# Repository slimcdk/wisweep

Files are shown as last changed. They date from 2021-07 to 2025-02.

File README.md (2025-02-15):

Feel free to support me and the development I do!

<a href="https://www.buymeacoffee.com/slimcdk" target="_blank">Buy Me A Coffee</a>

# WiSweep

Compact WiFi and Bluetooth (5.0) / ZigBee NEMA17 stepper controller featuring stall detection and ultra silent operation. Supply 5-36V upto 3A.

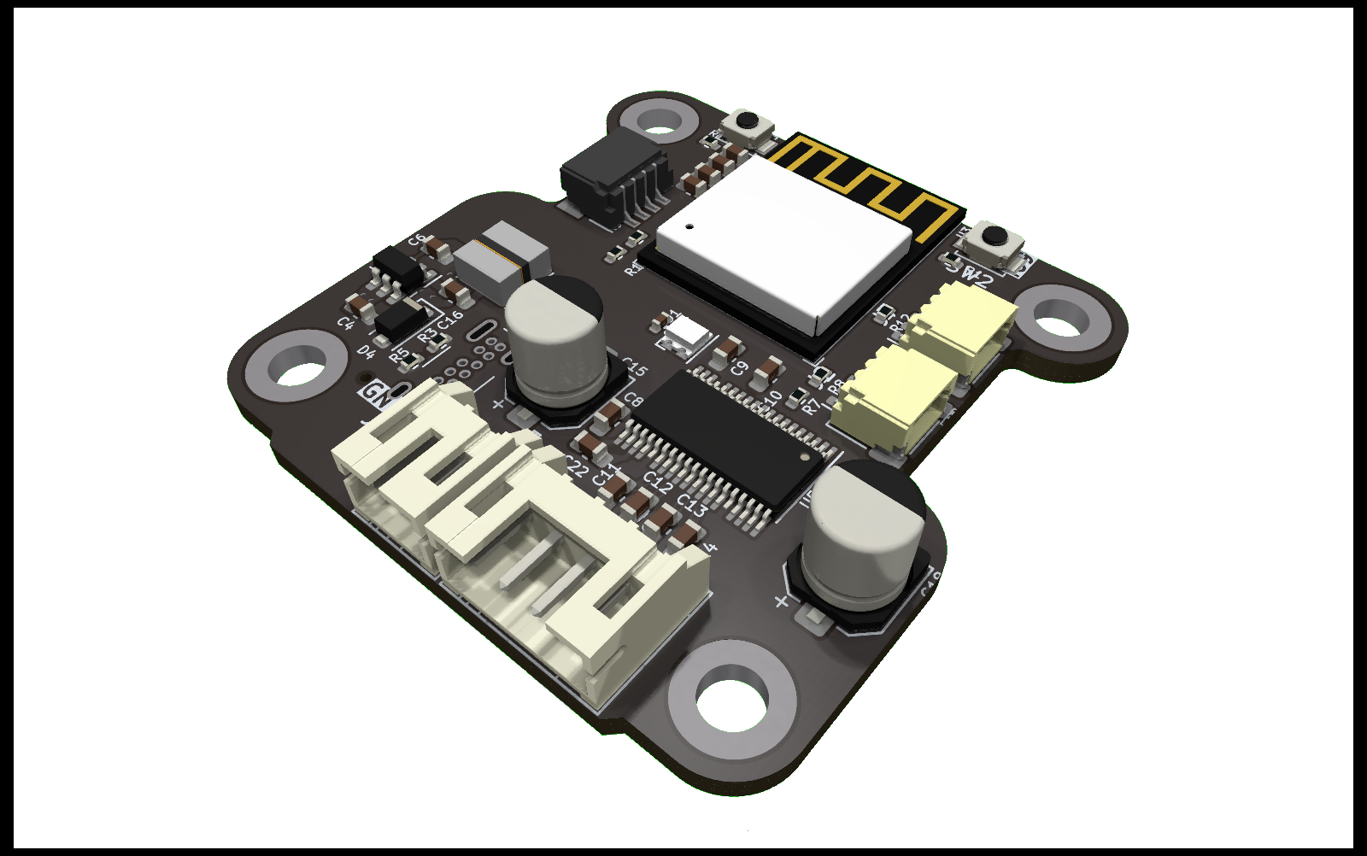
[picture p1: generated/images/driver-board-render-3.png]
the picture


## Production files



## Contribution

Clone repository and fetch submodules

```bash
$ git clone --recursive-submodules git@github.com:slimcdk/wisweep.git
```

## Versioning

Revisions are controlled through git tags such any production easily can be traced back to a commit containing everything. Complete sets of compatible schematics, PCB layouts, documentations, 3D models etc will all stay together under same tag in the source history.

---

## Software uses

* https://www.kicad.org/
* https://www.freecadweb.org/
* https://github.com/features/actions
  * https://github.com/INTI-CMNB/KiBot
* https://code.visualstudio.com/
  * https://marketplace.visualstudio.com/items?itemName=ms-vscode-remote.remote-containers

## Notes

### Parts

`VKMB1001H330MV` can be hard to source - `VKMB1001H220MV` (22µF variant) is an alternative.

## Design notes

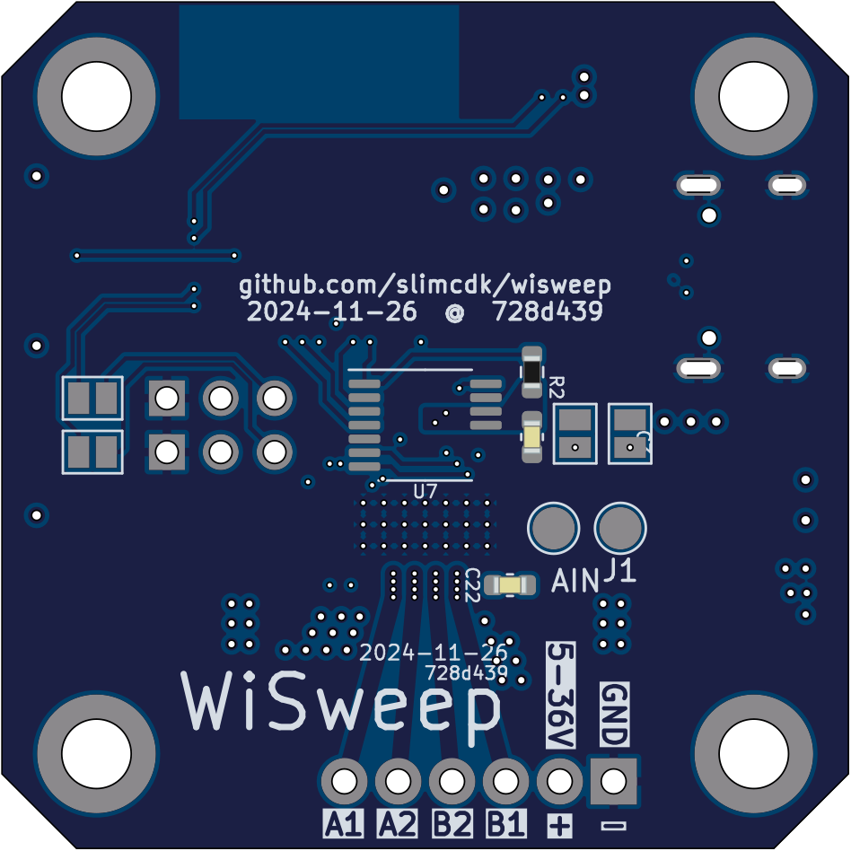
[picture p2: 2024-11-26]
generated/images/driver-board-bottom-view.png

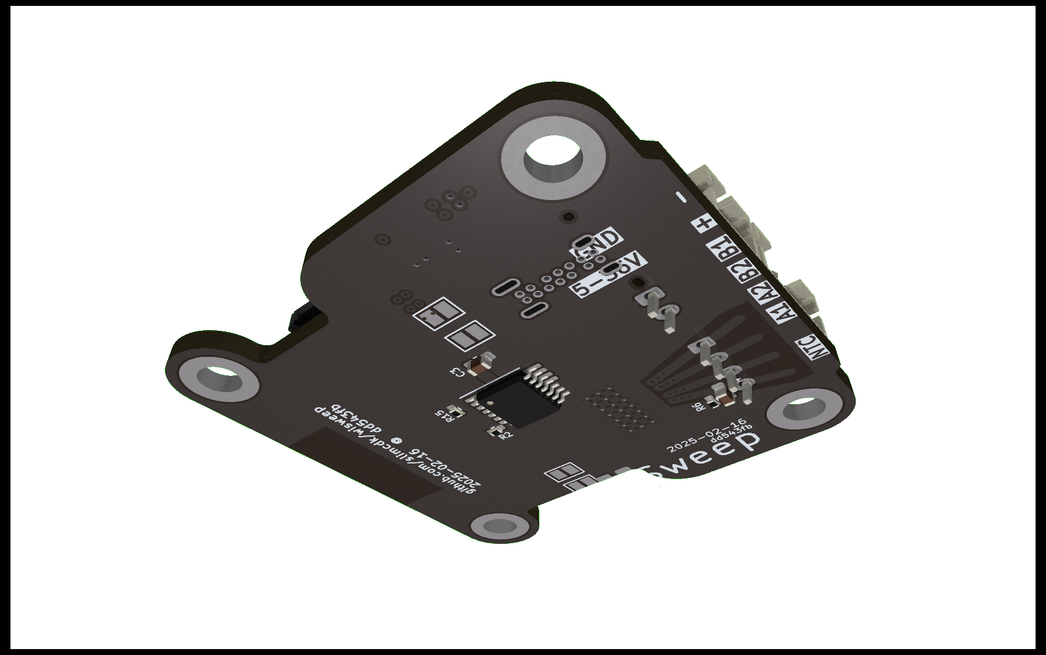
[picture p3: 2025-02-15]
generated/images/driver-board-render-5.png

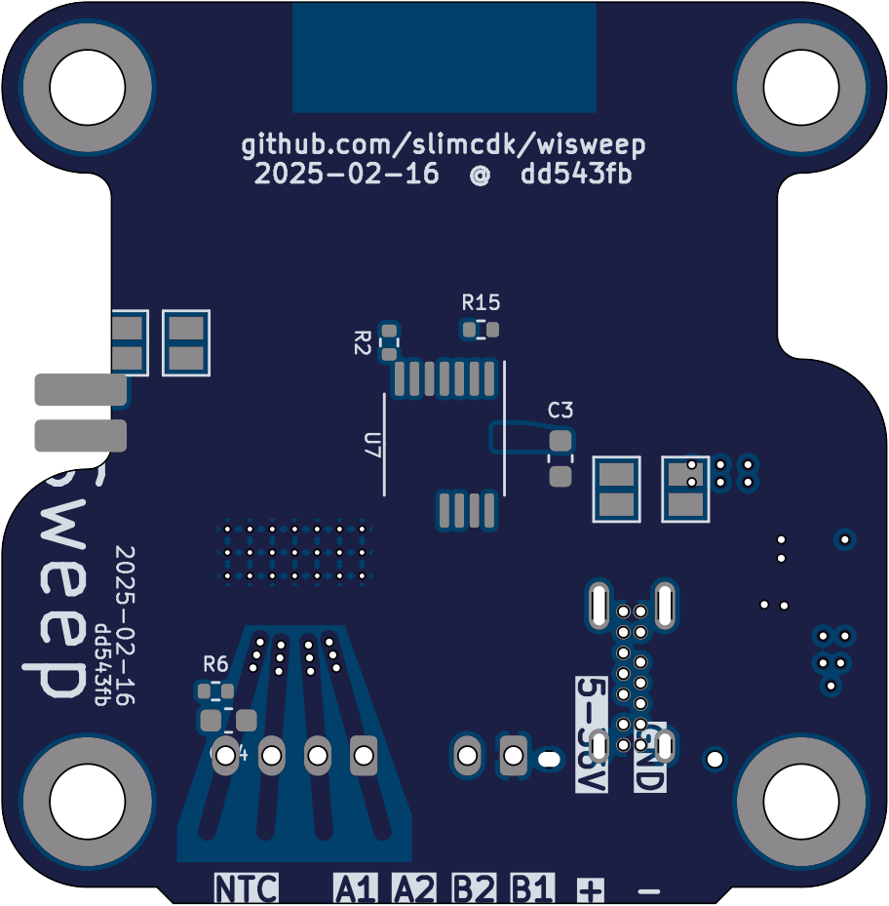
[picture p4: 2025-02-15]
generated/images/driver-board-bottom-view-no-comps.png

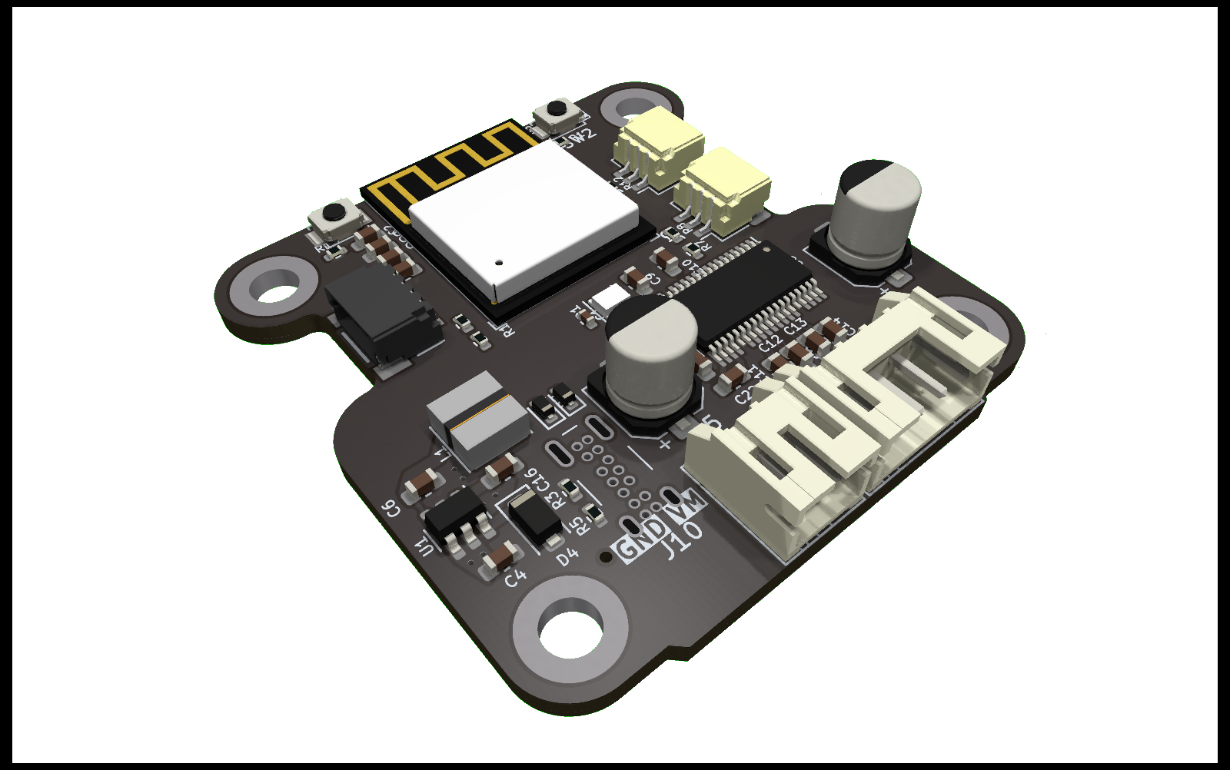
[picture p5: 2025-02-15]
generated/images/driver-board-render-4.png

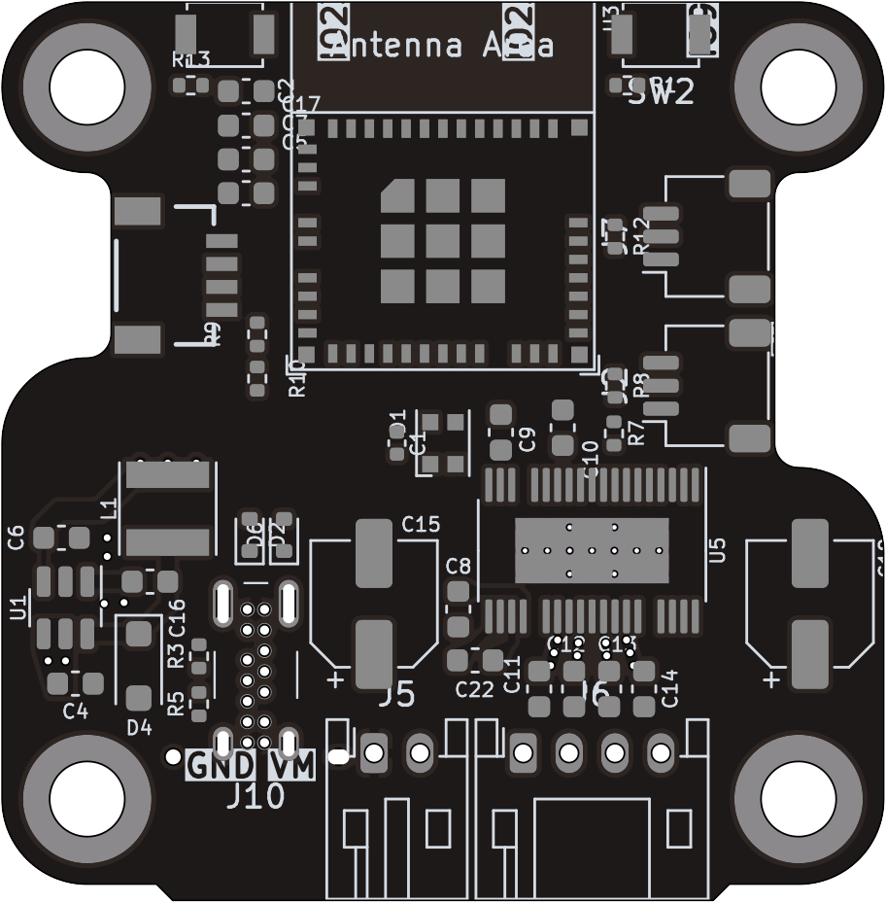
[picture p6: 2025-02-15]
generated/images/driver-board-top-view-no-comps.png

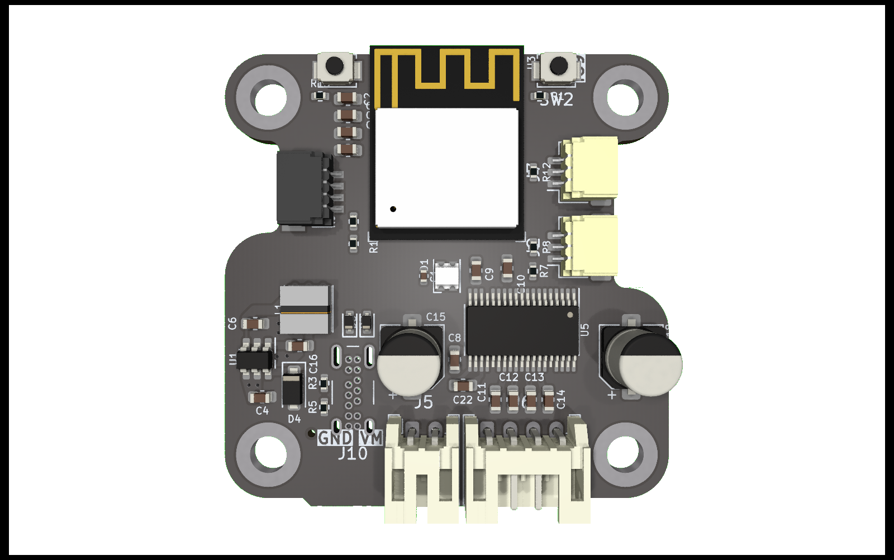
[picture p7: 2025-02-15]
generated/images/driver-board-render-1.png

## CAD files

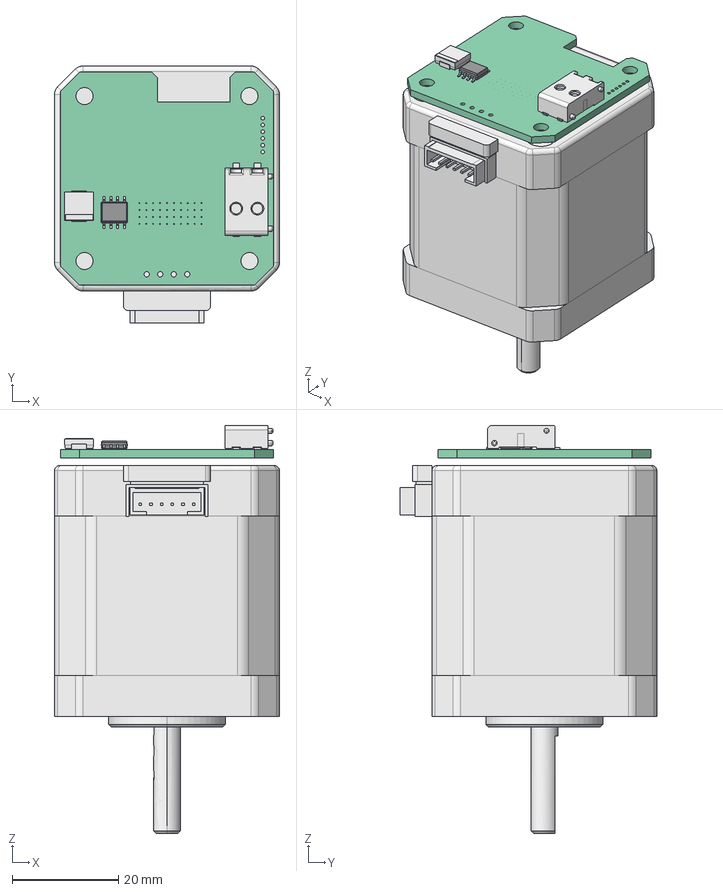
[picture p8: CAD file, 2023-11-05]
mechanics/assembly.FCStd
42.3 x 48.3 x 76.7 mm
Pulsivo_Stepper_17HS8401S
Pcb_5eb1
J1_C-2834006-2_000060e6b506[2]
BODY-SO
LEAD-SO
LEAD-SO001
LEAD-SO002
LEAD-SO003
LEAD-SO004
LEAD-SO005
LEAD-SO006
LEAD-SO007
THERMALPAD-SO

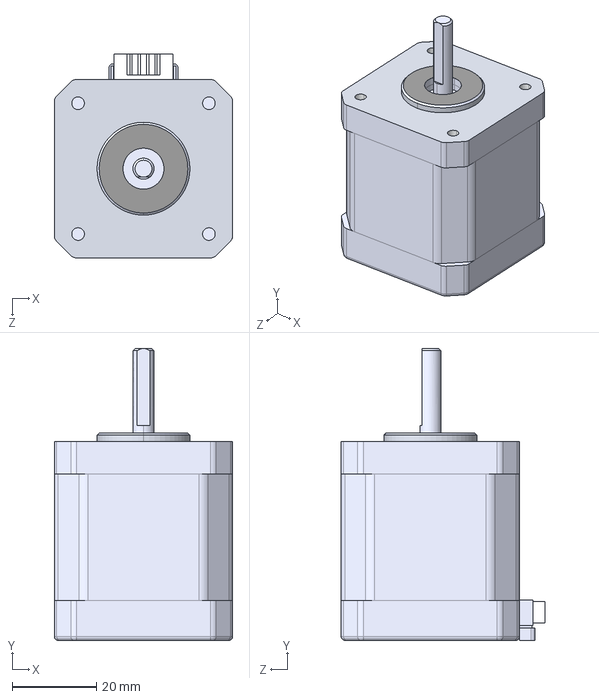
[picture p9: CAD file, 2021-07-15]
dependencies/3d-models/nema17-model/Pulsivo_Stepper_17HS8401S.IGS
42.3 x 69.2 x 48.3 mm

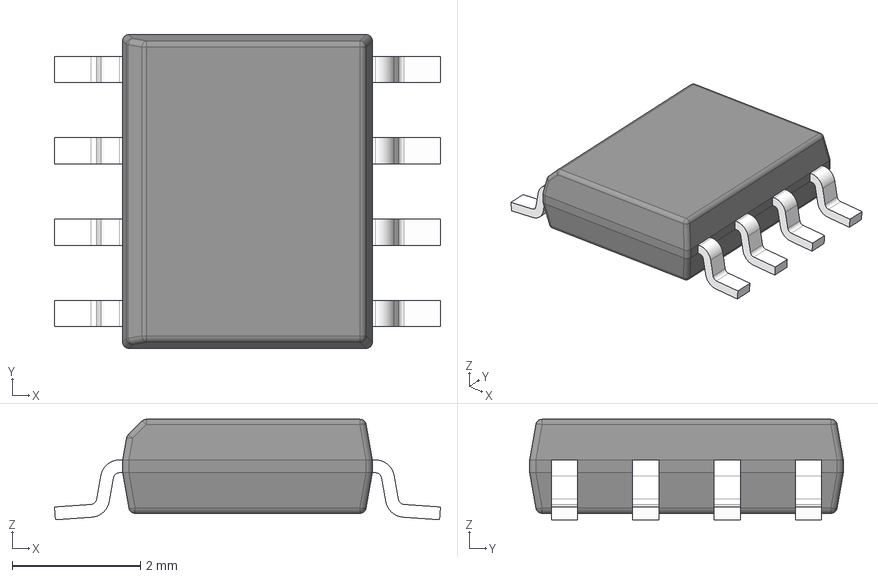
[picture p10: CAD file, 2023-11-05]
dependencies/3d-models/DDA0008B.stp
6.03 x 4.90 x 1.57 mm
BODY-SO
LEAD-SO x 8
THERMALPAD-SO

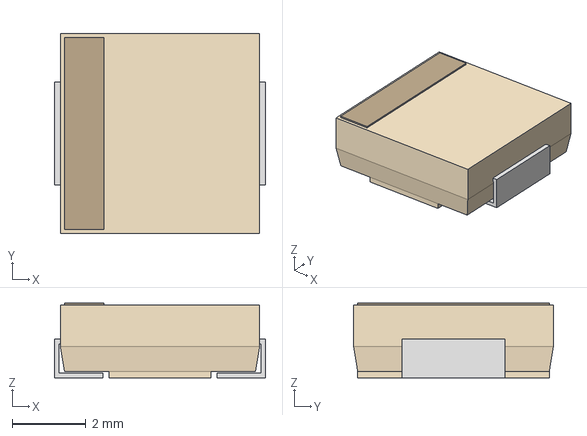
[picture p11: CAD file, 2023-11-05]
dependencies/3d-models/IND_IHLP_2020_BZ_VIS.step
5.74 x 5.44 x 2.03 mm

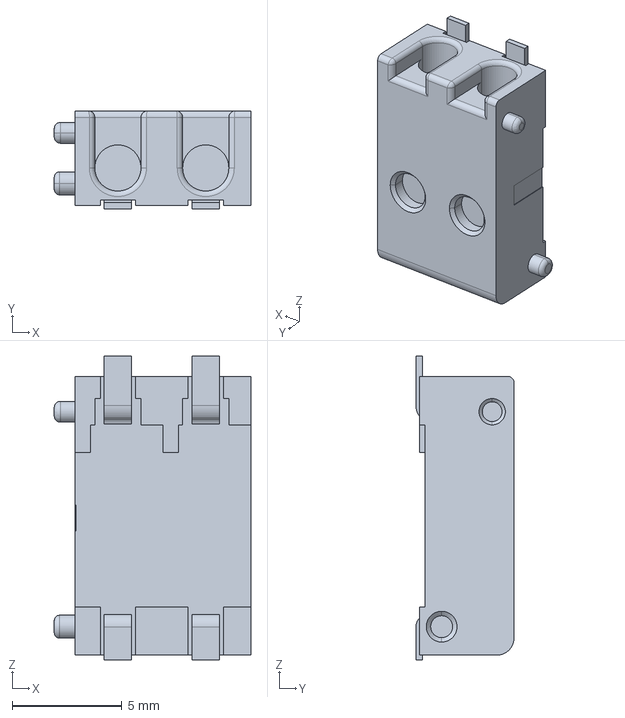
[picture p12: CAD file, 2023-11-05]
dependencies/3d-models/c-2834006-2-c-3d.stp
8.95 x 4.47 x 13.8 mm

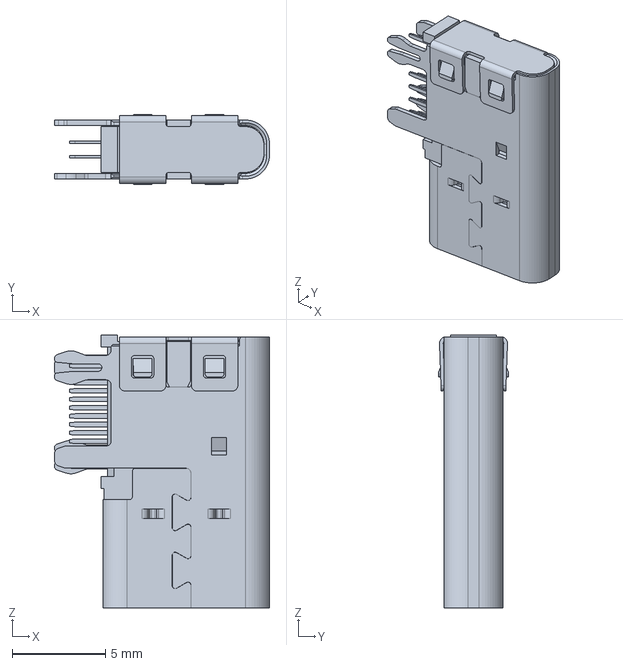
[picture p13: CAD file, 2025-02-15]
dependencies/3d-models/2169890001.stp
11.5 x 3.76 x 14.7 mm

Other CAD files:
dependencies/3d-models/nema17-model/Pulsivo_Stepper_17HS8401S.STL

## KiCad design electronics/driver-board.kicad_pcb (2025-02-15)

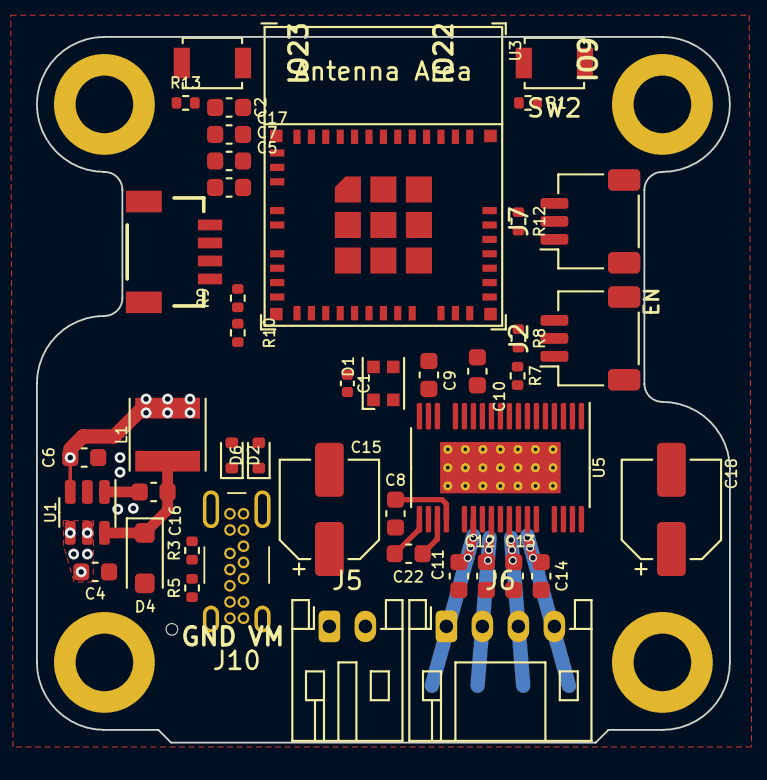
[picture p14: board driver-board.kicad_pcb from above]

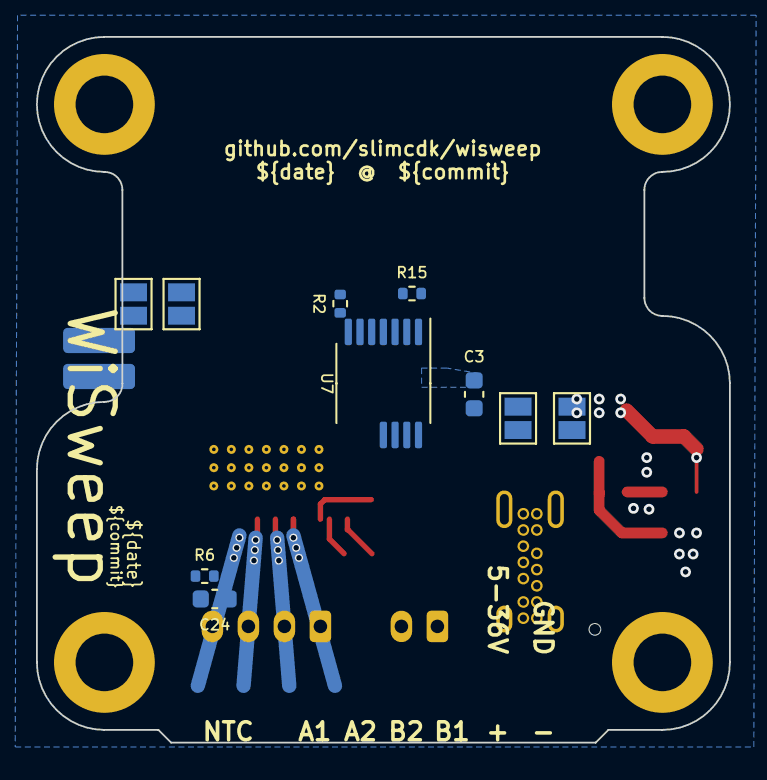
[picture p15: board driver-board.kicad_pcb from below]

Board: 4 copper layers, 38.5 x 39.2 mm, 58 parts (11 on the bottom side), 42 nets.

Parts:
C1: 100nF; C_0402_1005Metric
C2, C7, C8, C13, C14: 1µF; C_0603_1608Metric
C3, C9, C11, C12, C16, C17, C24: 100nF; C_0603_1608Metric
C4, C10: 2.2µF; C_0603_1608Metric
C5, C6: 10µF; C_0603_1608Metric
C15, C18: 33µF; CP_Elec_5x5.9
C22: 22nF; C_0603_1608Metric
D1: WS2812B; LED_WS2812B-2020_PLCC4_2.0x2.0mm
D2, D6: LESD5D5; D_SOD-523
D4: DS210W; D_SOD-123F
H1, H2, H3, H4: M3 MountingHole; MountingHole_3.2mm_M3_DIN965_Pad
J1: Conn_01x02; PinHeader_1x02_P2.00mm_Vertical_SMD_Pin1Left
J2, J7: Conn_01x03; JST_SH_SM03B-SRSS-TB_1x03-1MP_P1.00mm_Horizontal
J4: Qwiic_RA; JST_SMD_1.0mm-4_RA
J5: Conn_01x02; JST_PH_S2B-PH-K_1x02_P2.00mm_Horizontal
J6: Conn_01x04; JST_PH_S4B-PH-K_1x04_P2.00mm_Horizontal
J10: USB_C_Receptacle_USB2.0; USB_C_GT-USB-7036A
JP1, JP2, JP3, JP4: Jumper_2_Open; SolderJumper-2_P1.3mm_Open_Pad1.0x1.5mm
L1: 6.8µH; L_Vishay_IFSC-1515AH_4x4x1.8mm
R1, R2, R6, R8, R9, R10, R12, R13, R15: 10k; R_0402_1005Metric
R3, R5: 5k1; R_0402_1005Metric
R7: 12k; R_0402_1005Metric
SW1, SW2: SW_Push; SW_SPST_B3U-1000P
U1: LMR16006YQ3; SOT-23-6
U3: ESP32-C6-MINI-1/U; ESP32-C6-MINI-1
U5: TMC5240-TSSOP38; TSSOP-38_4.4x9.7mm_P0.5mm
U7: AS5047D; TSSOP-14_4.4x5mm_P0.65mm

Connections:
+3V3: C1.1, C3.2, C5.2, C6.2, C7.2, C9.2, C17.2, D1.1 (VDD), J2.2, J4.2, J7.2, L1.2, R1.2, R2.2, R6.2, R8.2, R9.2, R10.2, R12.2, R13.2, U1.3 (FB), U3.3 (3V3), U5.11 (VCC_IO), U7.11 (VDD), U7.12 (VDD3V3)
+5V: J10.A4 (VBUS), J10.A9 (VBUS), J10.B4 (VBUS), J10.B9 (VBUS)
/AS_ENCA: JP1.1 (A), U5.14 (ENCA), U7.7 (A)
/AS_ENCB: JP2.1 (A), U5.13 (ENCB), U7.6 (B)
/AS_ENCN: U5.12 (ENCN), U7.14 (I/PWM)
/ESP_BOOT: R1.1, SW2.2, U3.23 (GPIO9)
/ESP_EN: C2.1, R13.1, SW1.1, U3.8 (EN/CHIP_PU)
/ESP_GPIO0: R15.1, U3.12 (GPIO0/ADC1_CH0/XTAL_32K_P), U5.15 (DRV_EN)
/ESP_GPIO1: JP1.2 (B), U3.13 (GPIO1/ADC1_CH1/XTAL_32K_N)
/ESP_GPIO2: D1.4 (DIN), U3.5 (GPIO2/ADC1_CH2)
/ESP_GPIO3: JP2.2 (B), U3.6 (GPIO3/ADC1_CH3)
/ESP_GPIO4: U3.9 (MTMS/GPIO4/ADC1_CH4), U5.18 (DIAG1/SW)
/ESP_GPIO5: U3.10 (MTDI/GPIO5/ADC1_CH5), U5.17 (DIAG0)
/ESP_GPIO6: U3.15 (MTCK/GPIO6/ADC1_CH6), U5.2 (SDO/NAO), U7.3 (MISO)
/ESP_GPIO7: R2.1, U3.16 (MTDO/GPIO7), U7.1 (~CS)
/ESP_GPIO8: U3.22 (GPIO8), U5.38 (SCK/AD1), U7.2 (CLK)
/ESP_GPIO12: D2.2 (A2), J10.A7 (D-), J10.B7 (D-), U3.17 (GPIO12/USB_D-)
/ESP_GPIO13: D6.2 (A2), J10.A6 (D+), J10.B6 (D+), U3.18 (GPIO13/USB_D+)
/ESP_GPIO14: U3.19 (GPIO14), U5.1 (SDI/AD0), U7.4 (MOSI)
/ESP_GPIO15: U3.20 (GPIO15), U5.36 (CS/AD2)
/ESP_GPIO16: J4.4, R10.1, U3.31 (U0TXD/GPIO16)
/ESP_GPIO17: J4.3, R9.1, U3.30 (U0RXD/GPIO17)
/ESP_GPIO20: JP4.2 (B), U3.26 (GPIO20)
/ESP_GPIO21: JP3.1 (A), U3.27 (GPIO21)
/TMC_AIN: C24.2, J1.2, R6.1, U5.8 (AIN)
/TMC_OUT1A: J6.4, U5.32 (OUT1A)
/TMC_OUT1B: J6.2, U5.26 (OUT1B)
/TMC_OUT2A: J6.3, U5.30 (OUT2A)
/TMC_OUT2B: J6.1, U5.28 (OUT2B)
/TMC_REFL: J2.3, JP3.2 (B), R8.1, U5.5 (REFL)
/TMC_REFR: J7.3, JP4.1 (A), R12.1, U5.6 (REFR)
/USB_CC1: J10.A5 (CC1), R5.1
/USB_CC2: J10.B5 (CC2), R3.1
GND: C1.2, C2.2, C3.1, C4.1, C5.1, C6.1, C7.1, C9.1, C10.1, C11.2, C12.2, C13.2, C14.2, C15.2, C17.1, C18.2, C24.1, D1.3 (VSS), D2.1 (A1), D4.2 (A), D6.1 (A1), J1.1, J2.1, J4.1, J5.1, J7.1, J10.A1 (GND), J10.A12 (GND), J10.B1 (GND), J10.B12 (GND), R3.2, R5.2, R7.2, R15.2, SW1.2, SW2.1, U1.2 (GND), U3.1 (GND), U3.2 (GND), U3.11 (GND), U3.14 (GND), U3.36 (GND), U3.37 (GND), U3.38 (GND), U3.39 (GND), U3.40 (GND), U3.41 (GND), U3.42 (GND), U3.43 (GND), U3.44 (GND), U3.45 (GND), U3.46 (GND), U3.47 (GND), U3.48 (GND), U3.49 (GND), U3.50 (GND), U3.51 (GND), U3.52 (GND), U3.53 (GND), U5.3 (CLK), U5.10 (AGND), U5.27 (PGND1), U5.31 (PGND2), U5.39 (EP), U7.5 (TST), U7.13 (GND)
unnamed: C16.1, D4.1 (K), L1.1, U1.6 (SW)
unnamed: C16.2, U1.1 (CB)
unnamed: C22.2, U5.20 (CPI)
unnamed: C22.1, U5.22 (CPO)
unnamed: R7.1, U5.7 (IREF)
unnamed: C8.2, U5.23 (VCP)
unnamed: C10.2, U5.9 (VDD1V8)
VM: C4.2, C8.1, C11.1, C12.1, C13.1, C14.1, C15.1, C18.1, J5.2, U1.4 (~SHDN), U1.5 (VIN), U5.25 (VS1), U5.29 (VS2), U5.33 (VS3), U5.35 (SLEEP)

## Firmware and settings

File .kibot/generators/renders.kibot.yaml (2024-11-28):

kibot:
  version: 1

outputs:
  - type: step
    name: STEP model
    dir: exports
    options:
      output: "%f-%r.%x"
      metric_units: true

  - type: render_3d
    name: PCB 3D Render 1
    dir: exports/renders
    options:
      output: "%f-render-1.%x"
      height: 1000
      width: 1600
      zoom: -2
      download: true
      ray_tracing: true
      view: top
      transparent_background: true

  - type: render_3d
    name: PCB 3D Render 2
    dir: exports/renders
    options:
      output: "%f-render-2.%x"
      height: 1000
      width: 1600
      zoom: -2
      download: true
      ray_tracing: true
      view: bottom
      transparent_background: true

  - type: render_3d
    name: PCB 3D Render 3
    dir: exports/renders
    options:
      output: "%f-render-3.%x"
      height: 1000
      width: 1600
      zoom: -2
      download: true
      ray_tracing: true
      view: front
      rotate_x: -5
      rotate_y: 0
      rotate_z: 4
      move_y: 2
      transparent_background: true

  - type: render_3d
    name: PCB 3D Render 4
    dir: exports/renders
    options:
      output: "%f-render-4.%x"
      height: 1000
      width: 1600
      zoom: -2
      download: true
      ray_tracing: true
      view: front
      rotate_x: -5
      rotate_y: 0
      rotate_z: -4
      move_y: 2
      transparent_background: true

  - type: render_3d
    name: PCB 3D Render 5
    dir: exports/renders
    options:
      output: "%f-render-5.%x"
      height: 1000
      width: 1600
      zoom: -2
      download: true
      ray_tracing: true
      view: front
      rotate_x: 4
      rotate_y: 0
      rotate_z: -5
      move_y: -2
      transparent_background: true

  # - type: render_3d
  #   name: PCB 3D Render 6
  #   dir: exports/renders
  #   options:
  #     output: "%f-render-6.%x"
  #     height: 1000
  #     width: 1600
  #     zoom: -2
  #     download: true
  #     ray_tracing: true
  #     view: front
  #     rotate_x: -4.5
  #     rotate_y: 0
  #     rotate_z: 3
  #     move_y: 2
  #     transparent_background: true

  # - type: pcbdraw
  #   name: PCB Top View
  #   dir: exports/renders
  #   options:
  #     output: "%f-top-view.%x"
  #     format: png
  #     dpi: 600
  #     show_components: all

  - type: pcbdraw
    name: PCB Top View No Components
    dir: exports/renders
    options:
      output: "%f-top-view-no-comps.%x"
      format: png
      dpi: 600

  # - type: pcbdraw
  #   name: PCB Bottom View
  #   dir: exports/renders
  #   options:
  #     output: "%f-bottom-view.%x"
  #     format: png
  #     bottom: true
  #     dpi: 600
  #     show_components: all

  - type: pcbdraw
    name: PCB Bottom View No Components
    dir: exports/renders
    options:
      output: "%f-bottom-view-no-comps.%x"
      format: png
      bottom: true
      dpi: 600

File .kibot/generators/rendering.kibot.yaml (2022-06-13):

kibot:
  version: 1


outputs:
  - name: step
    type: step
    dir: exports
    options:
      metric_units: true
      
  - name: render top
    type: render_3d
    dir: exports/renders
    options:
      height: 1000
      width: 1600
      zoom: 2
      download: true
      ray_tracing: true
      view: top

  - name: render bottom
    type: render_3d
    dir: exports/renders
    options:
      height: 1000
      width: 1600
      zoom: 2
      download: true
      ray_tracing: true
      view: bottom

  - name: render angled
    type: render_3d
    dir: exports/renders
    options:
      height: 1000
      width: 1600
      zoom: 2
      download: true
      ray_tracing: true
      view: front
      rotate_x: -4
      rotate_y: 0
      rotate_z: -4

  - name: pcb_top
    type: pcbdraw
    dir: exports/renders
    options:
      output: "%f-%i.%x"
      format: jpg
      # show_components: none
      dpi: 600

  - name: pcb_bot
    type: pcbdraw
    dir: exports/renders
    options:
      output: "%f-%i.%x"
      format: jpg
      bottom: True
      # show_components: none
      dpi: 600

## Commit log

2021-07-07 Initial commit with existing project files
    [driver-board.kicad_pcb, driver-board.sch]
2021-07-07 Fixed references with external KiCAD library
    [driver-board.kicad_pcb, driver-board.sch]
2021-07-15 Added backpack template
    [backpack-board.kicad_pcb, backpack-board.sch]
2021-07-15 Work on schematics
    [Pulsivo_Stepper_17HS8401S.IGS, Pulsivo_Stepper_17HS8401S.STL, assembly.FCStd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]
2022-01-30 working on simplified design
    [assembly.FCStd, driver-board.kicad_pcb, driver-board.kicad_sch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]
2022-04-17 kicad 6; schematic updates; kicad deps update
    [driver-board.kicad_pcb, driver-board.kicad_sch, driver-board.sch]
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2022-04-17 updated external library collection
    [driver-board.kicad_sch]
2022-04-17 updated 3d models
    [driver-board.kicad_pcb, driver-board.kicad_sch]
2022-04-17 refresh 3d models
    [driver-board.kicad_pcb]
2022-04-23 work on external spram and pcb layout
    [assembly.FCStd, driver-board.kicad_pcb, driver-board.kicad_sch]
2022-04-25 couple of renders
    [driver-board.kicad_pcb, driver-board.kicad_sch]
2022-04-28 adjusting schematic and pcb component placement
    [driver-board.kicad_pcb, driver-board.kicad_sch]
2022-05-21 tmc2209 -> tmc 2226
    [driver-board.kicad_pcb, driver-board.kicad_sch]
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2022-05-24 date marker
    [driver-board.kicad_sch]
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2022-05-25 workflow kibot generate schematics with text replace
    [driver-board.kicad_sch]
2022-05-25 more kibot and exports
    [driver-board-B_Cu.gbr, driver-board-B_Mask.gbr, driver-board-B_Paste.gbr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]
2022-05-25 fixed schematic ref
2022-05-25 removed duplicate url. Removed secrets refs
    [driver-board.kicad_pcb, driver-board.kicad_sch]
2022-05-25 fixed schematic ref in readme
2022-05-26 hq renders
    [driver-board-B_Cu.gbr, driver-board-B_Mask.gbr, driver-board-B_Paste.gbr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]
2022-05-26 adjusting renders and readmne
    [driver-board-B_Cu.gbr, driver-board-B_Mask.gbr, driver-board-B_Paste.gbr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]
2022-05-28 adjusting gha
    [driver-board-B_Cu.gbr, driver-board-B_Mask.gbr, driver-board-B_Paste.gbr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]
2022-05-28 pcb layout redone
    [driver-board.kicad_pcb, driver-board.kicad_sch]
2022-06-06 adjusted tmc2209 circuitry and redid overall comp placement
    [driver-board.kicad_pcb, driver-board.kicad_sch]
2022-06-06 labels on pcb
    [driver-board.kicad_pcb]
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2022-06-07 another round of overall placement
    [driver-board.kicad_pcb, driver-board.kicad_sch]
2022-06-10 fixed duplicate usbc connector
    [driver-board.kicad_pcb]
2022-06-10 first tracing
    [driver-board.kicad_pcb, driver-board.kicad_sch]
2022-06-10 ore tracing
    [driver-board.kicad_pcb]
2022-06-12 first finished tracing; missing expboard connections and bom
    [driver-board.kicad_pcb, driver-board.kicad_sch]
2022-06-12 updated groundplanes
    [driver-board.kicad_pcb, driver-board.kicad_sch]
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2022-06-13 gh action and kibot
    [driver-board.kicad_sch, tmps8abvlhu.kicad_pcb]
2022-06-13 changed gpio for step/dir
    [driver-board.kicad_pcb, driver-board.kicad_sch, tmps8abvlhu.kicad_pcb]
2022-06-14 flipped symbol
    [driver-board.kicad_sch]
2022-06-14 moved internal traces to back layer
    [driver-board.kicad_pcb]
2022-06-14 exclude connectors from pcba fitting
    [driver-board.kicad_pcb]
2022-06-16 added info for BOM; redid some traces and labels
    [driver-board.kicad_pcb, driver-board.kicad_sch]
2022-06-18 replaced a few passive components and improved supply/common loop
    [driver-board.kicad_pcb, driver-board.kicad_sch]
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2023-08-07 work on module prototype
    [driver-board.kicad_pcb, driver-board.kicad_sch]
2023-11-05 tmc5240/ad5074d/esp32c6 board to be ordered
    [DDA0008B.stp, IND_IHLP_2020_BZ_VIS.step, assembly.FCStd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]
2023-11-05 fixing stuff
    [driver-board.kicad_pcb]
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2023-11-05 all vias have 0.3mm bore
    [driver-board.kicad_pcb]
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2023-11-05 hiding missing 3d models
    [assembly.FCStd, driver-board.kicad_pcb]
2023-11-05 changed thermal vias to 0.3mm bore
    [driver-board.kicad_pcb]
2023-11-05 updated vias to 0.25mm bore
    [driver-board.kicad_pcb]
2023-11-06 changed some 0402 caps to 0603
    [driver-board.kicad_pcb, driver-board.kicad_sch]
2023-11-06 changed motor connector to jst-xh
    [driver-board.kicad_pcb, driver-board.kicad_sch]
2023-11-06 trying to fix timeout
    [renders.kibot.yaml]
2023-11-06 filled in part numbers
    [driver-board.kicad_pcb, driver-board.kicad_sch]
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2023-11-07 renders without commit hash
    [driver-board.kicad_sch]
2023-11-07 tmc5240 datasheet; generated directory
    [driver-board.kicad_pcb, driver-board.kicad_sch]
2023-11-09 splitted power cap into two and changed connector to wago
    [driver-board.kicad_pcb, driver-board.kicad_sch]
2023-11-10 fixed tmc5240 fp and esp32 boot pins
    [driver-board.kicad_pcb, driver-board.kicad_sch]
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2023-11-14 new board layout; stripped 5v line and added qwiic and some buttons
    [driver-board.kicad_pcb, driver-board.kicad_sch]
2023-11-14 moved a few traces to give space for ground path
    [driver-board.kicad_pcb]
2023-11-14 pull ups for i2c; teardrops on through hole connections
    [driver-board.kicad_pcb, driver-board.kicad_sch]
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2023-11-15 fixed few connector part numbers
    [driver-board.kicad_pcb, driver-board.kicad_sch]
2023-11-20 new 3v3 power circuitry; renamed project
    [driver-board.kicad_pcb, driver-board.kicad_sch]
2023-11-21 moved few tracks and changed track width from 0.2 -> 0.25
    [driver-board.kicad_pcb, driver-board.kicad_sch]
2023-11-21 adjusting pnp file generation
    [driver-board.kicad_pcb]
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2023-11-30 changed rgb led and updated routing/tracks
    [driver-board.kicad_pcb, driver-board.kicad_sch]
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2023-11-30 moved more traces around
    [driver-board.kicad_pcb]
2024-11-25 incorporated USB port and refined board layout wip
    [driver-board.kicad_pcb, driver-board.kicad_sch]
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2024-11-28 fixed some broken references and kibot jobs
    [driver-board.kicad_pcb]
2024-11-28 fixed few render issues
    [driver-board.kicad_pcb]
2024-12-01 added ldo for USB
    [driver-board.kicad_pcb, driver-board.kicad_sch]
2024-12-01 added few ground vias
    [driver-board.kicad_pcb]
2024-12-11 reworked layout a bit
    [driver-board.kicad_pcb, driver-board.kicad_sch]
2025-02-15 wip usb jtag and power connectors
    [2169890001.stp, driver-board.kicad_pcb, driver-board.kicad_sch]
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

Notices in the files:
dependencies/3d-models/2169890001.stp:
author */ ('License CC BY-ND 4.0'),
